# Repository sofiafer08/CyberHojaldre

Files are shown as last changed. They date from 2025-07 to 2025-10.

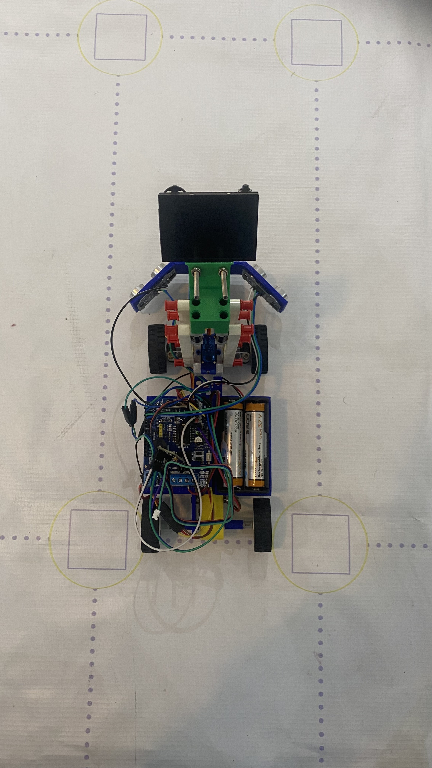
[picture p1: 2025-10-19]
V-photos/Top Angle.jpeg

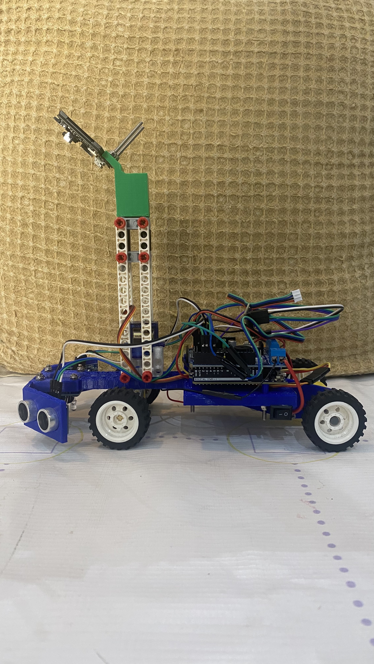
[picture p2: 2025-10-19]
V-photos/Right Angle.jpeg

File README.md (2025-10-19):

## CyberHojaldre - Future Engineers
<p>




encabezado github

## About Us

We are ***CyberHojaldre***, a dedicated team representing Thomas Jefferson School in the Future Engineers category of the WRO® 2025. Composed of Emilia Lever, Sofía Fernández, and Antonio Franco. This is our first year participating in this category and we are guided by our passion for robotics, comradery and are inspired by the 2025 season theme “The Future of Robots” —which explores how autonomous systems can shape tomorrow’s world, from smart cities and sustainable infrastructure to space exploration— we have embarked on an ambitious journey to design, build, and program an autonomous four-wheeled robotic vehicle capable of navigating a randomized course on its own. Together we have worked for months to bring our robot ***Captain ÑomÑom*** to life. Through the course of this competitions we have continuously refined our pre-existing skills, and have gotten the opportunity to expand our knowledge about electronics, mechanics, programming and teamwork.

>[!NOTE]
> We are always working on improving ***Captain ÑomÑom's*** performance! This means small tweaks are being made in every competition, which we may not be able to update immediately. 

marcos de fotos (1)

## Project Summary

Our robot, ***Captain ÑomÑom***, is designed to autonomously complete the driving challenge by detecting and avoiding obstacles in the track's controlled environment. The robot monitors track boundaries to ensure it stays within limits and maintains accurate navigation. It can also visually detect obstacles, allowing the robot to respond intelligently in real time by adjusting its path to avoid collisions depending on the obstacle's color. Beyond technical goals, one of our team's most important objectives is to enjoy the process, learn through experimentation and have fun building a robot that reflects both our creativity and our passion for robotics.

marcos de fotos (20)

## Past Projects

Before bringing ***Captain ÑomÑom*** to life, we had worked together to create a robot called ***POP*** -Short for People Is Nice-. It was able to complete the open course challenge and park in its starting position. He was built with the help of a 3D printed chassis and a sensor mount that complemented LEGO pieces. ***POP*** completed the course slowly yet accurately, but was unable to dodge obstacles. This is why we decided to start over with a new project a month before nationals. It would allow us to boost ***POP's*** ability allowing more speed, and a higher level performance. It involved replacing most components, programming from scratch, and changing the entire dynamic we had with our previous robot. This is how ***Captain ÑomÑom*** was born; thanks to an extensive creative process, and the merging of all our ideas. We are beyond excited for you to learn about all the specifications of ***Cap***. and hope you are able to see the technical growth required for the completion of this project. We keep ***POP*** in our hearts, and use him as inspiration for every cable wired and every line of code. Enjoy!

marcos de fotos (4)

## Team Members

| [**Sofía Fernández**](https://github.com/sofiafer08/CyberHojaldre/tree/main/Meet_the_Team#sofia-fernández) | [**Antonio Franco**](https://github.com/sofiafer08/CyberHojaldre/tree/main/Meet_the_Team#antonio-franco) | [**Emilia Lever**](https://github.com/sofiafer08/CyberHojaldre/tree/main/Meet_the_Team#emilia-lever) |
| :---: | :---: | :---: |
| *GitHub master, team spirit leader, and marketing director* | *Goofy designer and mechanics lead, invested in every part of the project* | *Silly, geeky programmer and electrician* | 
| <ins>16 years old</ins> | <ins>15 years old</ins> | <ins>16 years old</ins> |

## Table of Contents

* [`Code Explained`](./Code_Explained) This files contains an in-depth description on the way our program runs, and the process of making it. 
* [`Control Software`](./Control_Software) This file contains code of control software for all components which were programmed to participate in the competition.
* [`V-Photos`](./V-photos) Contains 6 photos of the vehicle (from every side, from top and bottom)
* [`Meet the Team`](./Meet_the_Team) Here you can find a short description of our team, who are our members, and several team photos. 
* [`Mobility Management`](./Mobility_Management) Inside it, are the strategic choices we made to achieve an efficient robot. 
* [`Models and Components`](./Models_&_Components) Here are all the 3D models designed by us to bring our robot to life, and a list of all its components. 
* [`Power and Sense Management`](./Power_&_Sense_Management) Inside this file is the description of the electrical distribution of our robot. 
* [`Schemes`](./Schemes) This file contains one or several schematic diagrams in form of JPEG, PNG or PDF of the electromechanical components illustrating all the elements (electronic components and motors) used in the vehicle and how they connect to each other.
* [`Vehicles Photos`](./V-photos/) Here you can find multiple photos of our robot taken from different perspectives (from every side, top and bottom. 
* [`Performance Video`](./Video) This file contains the performance video of our robot during the open course.

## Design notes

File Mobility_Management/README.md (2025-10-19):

# Mobility Management

## General Vehicle Design

The robotic vehicle is constructed upon a **3D printed PETG chassis**. It's powered through the rear axle using a **3V–6V Dual Axis TT Gear Motor** and steered with a **SG90 9g Micro Servo**. It counts with two **HC-SR04 Ultrasonic Distance Sensors** to detect the track's walls in order to avoid collisions, a **HUSKYLENS Smart Vision Sensor** to detect incoming traffic signs and identify their color and a **TCS3200 Color Sensor Module** which serves as a backup for the camera. All systems are controlled by an **Arduino UNO R4 WiFi** with a **Module L298P Motor Shield HW-723**.

## Drivetrain

### Rear-Wheel Drive

We power our drivetrain using a **3V–6V Dual Axis TT Gear Motor**, which is directly connected to the vehicle's rear axle. Our rear axle is responsible for the forward and backward motion on our robot. This rear wheel drive design eliminates the necessity for complex systems such as constant velocity (CV) joints or external gearboxes without sacrificing torque, speed, and traction; resulting in a reliable and easy to repair robot.

marcos de fotos (10)

### Steering

We use an **Ackermann steering** built using LEGO parts. This steering system is proven to be one of the most efficient and reliable which is demonstrated by its years of use in the automotive industry. The Ackermann principle ensures that a vehicle's inner front wheel turns at a greater angle than the outer front wheel during a turn, allowing both wheels to trace concentric circles around a single virtual pivot point. We control the steering using degrees thanks to the **SG90 9g Micro Servo**, which makes it easier to program and improves the robot's accuracy. This steering system also provides a wide range of movement, making the vehicle highly maneuverable.

marcos de fotos (11)

## 3D Printed Parts

### Chassis

We use a custom **3D printed PETG chassis** designed using Fusion 360. This vehicle frame is custom fitted with a space for our **two Slot 18650 Battery Holder**, an **Arduino UNO R4 WiFi** holder, a bracket for our **3V–6V Dual Axis TT Gear Motor**, a LEGO compatible 3x9 Technic axle hole plate to secure our steering's **SG90 9g Micro Servo's LEGO mount** and the **HUSKYLENS Smart Vision Sensor's** mount, holes for our **HC-SR04 Ultrasonic Distance Sensors** and a mount for our **TCS3200 Color Sensor Module**. This simple design gives us ease of repair, high ground clearance and torsional rigidity. It's an effective design which adapts to our robot's needs.

For more information, [*click here*](https://github.com/sofiafer08/CyberHojaldre/blob/main/Models_%26_Components/Chassis.stl) to open the Chassis Interactive stl.

marcos de fotos (5)

### Rear Axle Adapters

In order to directly connect our **3V–6V Dual Axis TT Gear Motor** to the vehicle's rear axle, we designed two **3D printed PETG adapters**. From one side, the adapter is able to connect to the **3V–6V Dual Axis TT Gear Motor's** axle, while from the other its able to couple with a LEGO Technic axle, allowing us to use LEGO wheels and tires to provide traction.

For more information, [*click here*](https://github.com/sofiafer08/CyberHojaldre/blob/main/Models_%26_Components/tt_Motor_Axle.stl) to open the Motor Axle Interactive stl

marcos de fotos (7)

### Camera Mount

The HUSKYLENS Smart Vision Sensor is installed in a 3D printed PETG camera mount. This mount allows us to have a greater height and position the camera at a 45° angle during the robot’s testing in order to enhance the range and accuracy. We connect it to the chassis LEGO pins, as both 3D printed pieces have LEGO compatibility. This modular piece amplifies the number of uses our camera has, changing the robot’s capacities.

For more information, [*click here*](https://github.com/sofiafer08/CyberHojaldre/blob/main/Models_%26_Components/HuskyLens_Mount.stl) to open the HuskyLens Mount Interactive stl.

marcos de fotos (8)

### Servo LEGO Mount

We also used the bottom part of a **SG90 9g Micro Servo LEGO mount** designed by **wilix from Thingyverse**. This mount enabled us to connect the servo's axle to our LEGO steering, giving us a great mix of efficiency and compatibility.  

For more information, [*click here*](https://www.thingiverse.com/thing:4303585) to visit the wilix's Thingyverse page.

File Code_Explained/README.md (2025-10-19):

## Open Challenge Programming

For our previous robot we programmed using MakeCode for microbit. It consisted of a simple code that would rotate the servo to 210 degrees if the left ultrasonic sensor percieved a distance less than 45cm. The same would happen with the right ultrasonic sensor, but in that case the servo will rotate to 150 degrees. In the case that both sensors read a distance greater than 30cm, the servo was set to 180 degrees and it would continue its straight path. Once the time variable ended, the DC motor would be stopped, and our robot would park in the position it started. 

Since we developed **Captain ÑomÑom**, We have now programmed a new code that includes other components that facilitate Cap.'s cruising. 

*   The code begins by establishing where all the physical components like motors and sensors are connected. It also sets important constants that act as the robot's rules of operation:

      *   **Max Sequences:** Dictates the total number of times the robot will perform  the color detection and then turn. When it reaches this number Cap. will shut down.
      *   **Reset Delay:** The brief pause the robot takes after reacting to a color before it's ready for the next one. This ensures Cap. will read only one color when he gets to the turns. Without it, he would detect both blue and orange and would turn in oppossite directions, steering him away from his course.
      *    **Shutdown Delay:** The amount of time the robot waits after its final sequence before turning off its motor. With this fuction, we can ensure Cap. reaches it original position and doesnt stop suddenly in the middle of a turn.
      *  **Steering Range:** The servo motor's movement is limited to a safe range where we have the MAX and MIN angles, 108 and 78 degrees accordingly, to prevent the robot from making overly sharp turns. 

*   **Sensors & Perception:**
    *   The robot relies on two main sensing systems that work together:
        *   **HuskyLens Camara:** This is the primary component of the code. It is trained to recognize organge and blue to perform the turns and not rely solely on ultrasonic sensors. When it detects blue, it commands a left turn. When it detects oragne, it commands a right turn.
        *   **Ultrasonic Sensors:** These act as a secondary system for obstacle avoidance. If Cap. gets too close to a side of the walls, the ultrasonic sensors will help him stay centered, and avoid crashing. 

*   **Startup Sequence:**
    *   When powered on, the robot pauses for 3 seconds to ensure all systems are ready.
    *   It then checks for the HuskyLens camera and prepares it for color detection.

*   **Main Operation Loop:**
    *   The core of the code is a loop that constantly checks a specific order of events:
        1.  **Shutdown Check:** It first checks if the maximum number of sequences has been reached to begin the shutdown process. This number is 12, seeing as Cap. would need to detect the color 12 times in order to complete three full rounds. 
        2.  **Color Detection:** If it hasn't reached the max number of sequences (12 detections), it prioritizes looking for the colored lines. When a color is spotted, it executes the corresponding turn, atllies up the sequence, and temporarily pauses further color detection for 2 seconds.
        3.  **Obstacle Avoidance:** While paused for color detection (or when no color is seen), the ultrasonic sensors remain active to avoid bumps.
        4.  **Reset:** After the reset delay, the robot centers its wheels and resumes looking for colors, continuing the cycle until its task is complete.

* Once it completes the three rounds the servo is set back to 90 degrees so that it will go straight for a few seconds more and park in its original position bringing us to the end of our Open Course Code. 

## Obstacle Challenge Programming

### **Course Explanation: Obstacle Avoidance & Navigation**

The code begins by establishing where all the physical components like motors, sensors, and camera are connected. It also sets important constants that act as the robot's rules of operation:

*   **Max Sequences:** Dictates the total number of times the robot will perform a primary color detection and turn sequence. When it reaches this number, the robot will shut down.
*   **Color Detection Pause:** A 6-second period after detecting a blue or orange line where the robot ignores further blue/orange detections. This ensures it completes its turn and reverse maneuver without being interrupted. During this pause, it can still detect and react to red and green obstacles.
*   **Steering Angles:** The robot uses two sets of turning angles. **Sharp turns** are used during the initial setup and for quick ultrasonic obstacle avoidance. **Mild turns** are used for the main course navigation, providing smoother and more controlled turns around obstacles and after detecting lines.
*   **Ultrasonic Threshold:** The minimum distance, in centimeters, at which the robot considers an object an obstacle and will initiate an avoidance turn.

*   **Sensors & Perception:**
    *   The robot relies on two main sensing systems that work together:
        *   **HuskyLens Camera:** This is the primary sensor for navigation. It is trained to recognize four colors:
            *   **Blue & Orange:** These are the *primary navigation lines*. They signal the robot to execute a turn sequence, bump into the wall behind it, and then continue, effectively moving it to the next section of the course.
            *   **Red & Green:** These act as *virtual obstacles*. When detected, the robot performs an avoidance maneuver by backing up and turning left and right to navigate around them.
        *   **Ultrasonic Sensors:** These act as a secondary, physical safety system for obstacle avoidance. If the robot gets too close to a wall or object on its left or right side, these sensors will command a mild turn to keep it centered and avoid crashes.

*   **Startup Sequence:**
    *   When powered on, the robot initializes its motors, servo, and sensors.
    *   It performs an initial environmental check using the ultrasonic sensors to ensure it has space to operate.
    *   It then checks for the HuskyLens camera and prepares it for color detection.

*   **Main Operation Loop:**
    *   The loop constantly checks a specific order of events:
        1.  **Shutdown Check:** It first checks if the maximum number of sequences has been reached to begin the shutdown process.
        2.  **Continuous Ultrasonic Monitoring:** The ultrasonic sensors are the least important part of the code. If a wall is detected, the robot turns mildly away from it, and then continues forward. This is done to avoid walls in case Cap. gets too close to them. This is vital to ensure the HuskyLens has a clear view of all the obstacles. If it's too close to one side, it's possible he’ll miss the detection of certain obstacles.
        3.  **Color Detection & Reaction:** The robot simultaneously looks for colors. He has two given instructions in case he detects one of the two possible sets of colors:
            *   **Blue/Orange:** The robot will continue a forward motion for a few seconds longer, sort of a delay before turning. This is so that he has advanced enough to turn and bump into the wall behind him. He first turns in the corresponding direction, then reverses to bump into the wall. This way, he can always center himself and is awa.re of all the objects in front of him. This prevented him from turning too sharply or too widely and missing obstacles around him. When completing this sequence, he also tallies it up so as to keep track of how many laps are missing. Once he reaches 12, he will stop. Lastly, after the detection of one of the colored lines, he enters a pause period where it ignores further blue/orange lines so as to not detect the same line when going forward again.

            *   **Red/Green:** This feature allows him to avoid obstacles. When detecting either green or red, he stops, reverses briefly so as to not bump into the obstacle, and then performs a sequenced turn (left-then-right or right-then-left) to navigate around the virtual obstacle before continuing forward. When he makes this maneuver he ensures the obstacle is avoided, but also places himself back in his path.

*   Once the robot completes its maximum number of sequences (12), it stops its motor, bringing the course run to a complete end.

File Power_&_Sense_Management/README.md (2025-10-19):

Power and Sensor Management
===

## Power Source

### Batteries

The power source of ***Captain ÑomÑom*** are **two 18650 Rechargeable Lithium-Ion Batteries**, each with a nominal voltage of **3.7Vdc** and a storage capacity of **2800 mAh**. They are coupled on a **two slot 18650 Battery Holder** which is connected to the VMS (power input) and GND (negative ground connection) ports on our **Module L298P Motor Shield HW-723**. The shield regulates the voltage to 5Vdc before supplying power to our **Arduino UNO R4 WiFi**. Then, through our shield's 5V ports, we supply both of our **HC-SR04 Ultrasonic Distance Sensors**, our **HUSKYLENS Smart Vision Sensor**, our **TCS3200 Color Sensor Module**, our **SG90 9G Micro Servo** and our **3Vdc ~ 6Vdc Dual Axis TT Gear Motor**.

rechargeable-li-ion-battery 200

**Key Specifications:**
* **Nominal Voltage:** 3.6 Vdc ~ 3.7 Vdc
* **Nominal Capacity:** 2800 mAh
* **Cycle Life:** ~500 cycles (to 80% capacity)

For more information, [*click here*](https://www.tinytronics.nl/product_files/004721_TENPOWER_INR18650-28HE_datasheet.pdf) to open the 18650 Rechargeable Lithium-Ion Battery's datasheet.

## Sensors

### Ultrasonic Sensors

We used two **HC-SR04 Ultrasonic Distance Sensors**. Each sensor provides **2cm to 400cm** of non-contact measurement functionality with a ranging accuracy that can reach up to **3mm**. Each HC-SR04 module includes an ultrasonic transmitter, a receiver and a control circuit. We placed a sensor on each side (left and right) of our autonomous vehicle. Their purpose is to detect the track's walls in order to avoid collisions.

ultrasonic sensor 200

**Key Specifications:**
* **Operating Voltage:** 3.3Vdc ~ 5Vdc
* **Quiescent Current:** <2mA
* **Operating Current:** 15mA
* **Operating Frequency:** 40KHz
* **Operating Range & Accuracy:** 2cm ~ 400cm ( 1in ~ 13ft) ± 3mm
* **Sensitivity:** -65dB min
* **Sound Pressure:** 112dB
* **Effective Angle:** 15°
* **Connector:** 4-pins header with 2.54mm pitch
* **Dimension:** 45mm x 20mm x 15mm
* **Weight:** 9g

For more information, [*click here*](https://www.handsontec.com/dataspecs/HC-SR04-Ultrasonic.pdf) to open the HC-SR04 Ultrasonic Distance Sensor's datasheet.

### Color Sensor

We used a **TCS3200 Color Sensor Module**. The sensor can detect a wide variety of colors based on their wavelength. This sensor is specially useful for color recognition projects such as color matching and color sorting. Each TCS3200 module includes an array of photodiodes, filters for different colors, and a control circuit. Its purpose is to detect the diagonal lines which merge on the track's walls in order to make precise turns.

color sensor 200

**Key Specifications:**
* **Operating Voltage:** 2.7Vdc ~ 5.5Vdc
* **Photodiodes:** 64 total (16 red, 16 green, 16 blue, 16 clear)
* **Operating Range & Accuracy:** Best at 1–3 cm from the object
* **Extras on module:** Includes 4 white LEDs for consistent illumination

For more information, [*click here*](https://www.mouser.com/catalog/specsheets/tcs3200-e11.pdf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) to open the TCS3200 Color Sensor Module's datasheet.

>[!NOTE]
> We are currently not implementing this sensor as part of our code. We decided to replace its original function with the HuskyLens. Nonetheless, it still remains as part of our robot in case a minor inconvenience occurs. 
### HuskyLens Camera

We used a **HUSKYLENS Smart Vision Sensor**. This sensor can detect and recognize objects, faces and colors using built-in AI algorithms. It is especially useful for projects involving computer vision, such as object tracking and autonomous navigation. Each HUSKYLENS module includes a camera, a processor for AI functions and an interface with a digital display and buttons. Its purpose is to detect incoming traffic signs and identify their color in order to indicate the vehicle side of the lane it must follow in the obstacle challenge.

Husky lens 200

**Key Specifications:**
* **Processor:** Kendryte K210
* **Image Sensor:** OV2640 (2.0 Megapixel Camera)
* **Operating Voltage:** 3.3Vdc ~ 5Vdc
* **Current Consumption (TYP):** 320mA 3.3Vdc, 230mA 5Vdc (face recognition mode; 80% backlight brightness; fill light off)
* **Connection Interface:** UART, I2C
* **Display:** 2in IPS screen with 320 x 240 resolution
* **Built-in Algorithms:** Face Recognition, Object Tracking, Object Recognition, Line Tracking, Color Recognition, Tag Recognition
* **Dimension:** 52mm x 44.5mm

For more information, [*click here*](https://www.farnell.com/datasheets/3178377.pdf) to open the HUSKYLENS Smart Vision Sensor.

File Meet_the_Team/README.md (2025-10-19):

Meet the members of our team
===

## Sofia Fernández

<p align='justify'>My name is Sofia Fernandez, I'm a 16-year-old girl from Honduras currently living in Panama. I moved here last year in search of better opportunities, and since then, I've discovered a passion for robotics and everything related to STEM. This new environment has inspired me to keep learning, growing, and exploring all the possibilities within science, technology, engineering, and math. I'm always looking for ways to expand my knowledge and take on new challenges in the STEM world.</p>  

marcos de fotos (14)

## Antonio Franco 

<p align='justify'>My name is Antonio Franco, I'm a 15-year-old boy born in Panama. I've shared a passion for STEM and engineering from an early age, making my career in robotics very vast. In my path, I've discovered that Computer Aided Design or CAD is my main talent, which I've incorporated in each one of my projects. Competitions like FRC or WRO are constant challenges for my skills, which inspire me each day to aim higher and to prove I'm capable of achieving success. STEM always keeps me growing and improving, and I always look forward to challenging myself with each project.</p>  

marcos de fotos (19)

## Emilia Lever 

<p align='justify'>Hello! My name is Emilia, and I´m 16-years-old. I have always enjoyed participating in as many activities as possible, which led to the development of a variety of hobbies such as knitting, dancing, theater, debate, etc. As I've dipped my toes into the different pools of extracurriculars, I discovered a deep love towards the STEM community. I have since been a part of many robotic groups in a diverse range of competitions with a specific passion for the math olympics, even reaching silver and bronze medals. I hope to continue expanding my knowledge and skills with the help of my mentors and teammates, and will forever encourage people to give the STEM world a chance to win their hearts over.</p>  

marcos de fotos (16)

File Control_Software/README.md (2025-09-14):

Control software
====

This directory contains the code for both the Open and Obstacle Course. You can find the code written in C++ coded in the platform ARDUINO.IDE.
An explanation about our coding decisions can be found in [Code Explained](https://github.com/sofiafer08/CyberHojaldre/tree/main/Code_Explained) .

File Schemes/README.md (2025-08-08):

Electromechanical diagrams
====

This directory contains one schematic diagrams in the form of a PNG of the electromechanical components illustrating all the elements (electronic components and motors) used in the vehicle and how they connect to each other.

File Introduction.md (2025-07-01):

Future Engineers
====

* We are Emilia Lever, Sofia Fernandez, and Antonio Franco, a dedicated team representing the Thomas Jefferson School in the Future Engineers category of the WRO® 2025. Guided by our passion for robotics and inspired by the 2025 season theme “The Future of Robots”—which explores how autonomous systems can shape tomorrow’s world, from smart cities and sustainable infrastructure to space exploration—we have embarked on an ambitious journey to design, build, and program an autonomous four-wheeled robotic vehicle capable of navigating a randomized course on its own.

## Content

* `t-photos` contains 2 photos of the team (an official one and one funny photo with all team members)
* `v-photos` contains 6 photos of the vehicle (from every side, from top and bottom)
* `video` contains the video.md file with the link to a video where driving demonstration exists
* `schemes` contains one or several schematic diagrams in form of JPEG, PNG or PDF of the electromechanical components illustrating all the elements (electronic components and motors) used in the vehicle and how they connect to each other.
* `src` contains code of control software for all components which were programmed to participate in the competition
* `models` is for the files for models used by 3D printers, laser cutting machines and CNC machines to produce the vehicle elements. If there is nothing to add to this location, the directory can be removed.
* `other` is for other files which can be used to understand how to prepare the vehicle for the competition. It may include documentation how to connect to a SBC/SBM and upload files there, datasets, hardware specifications, communication protocols descriptions etc. If there is nothing to add to this location, the directory can be removed.

## Robot Objectives

## Mobility Management

Our robot, "POP", short for People is nice, works with the help of two motors. For the movement of the rear-axle we implemented a red "GeekServo" direct current (DC) motor, we chose it since it has a strong online community that already implements this motor using micro:bit software and hardware. It also has LEGO compatability, making it easier to adapt to our design. Our robot POP has a gray "GeekServo" servo motor as well. This controls the front-axle and provides the high-precision that is needed. This motor allows us to program it using degrees, which fits our team's need for accuracy.

The design of our chassis was made from scratch using Autodesk Fusion 360. Since the motors we agreed upon were compatible with LEGO components, it was only natural that our design was based on these same pieces. We have a simple structure inspired on a ladder-frame chassis, since our main objectives can be accomplished with a reliable base.

## Power and Sensor Management
## Obstacle Management
## Open Challenge Programming
## Programming Challenge Obstacles
## Components 

POP has a variety of parts that make up both his hardware and software. This includes:

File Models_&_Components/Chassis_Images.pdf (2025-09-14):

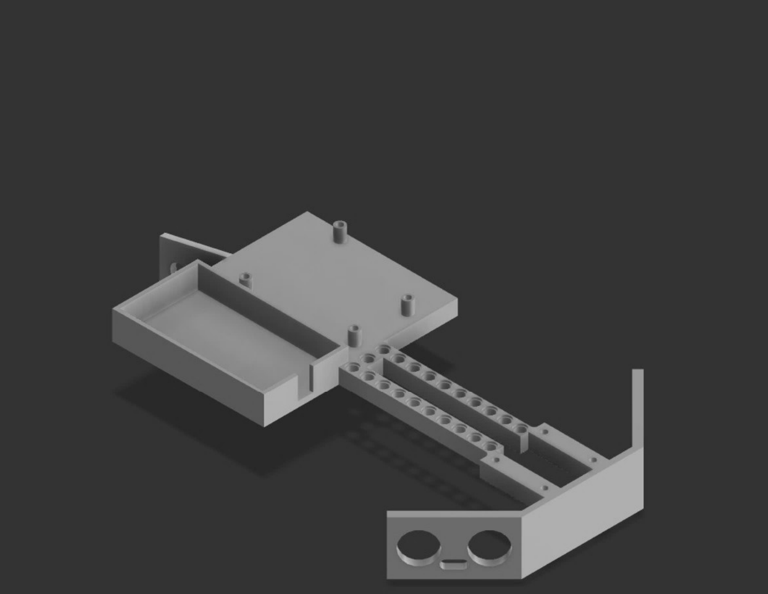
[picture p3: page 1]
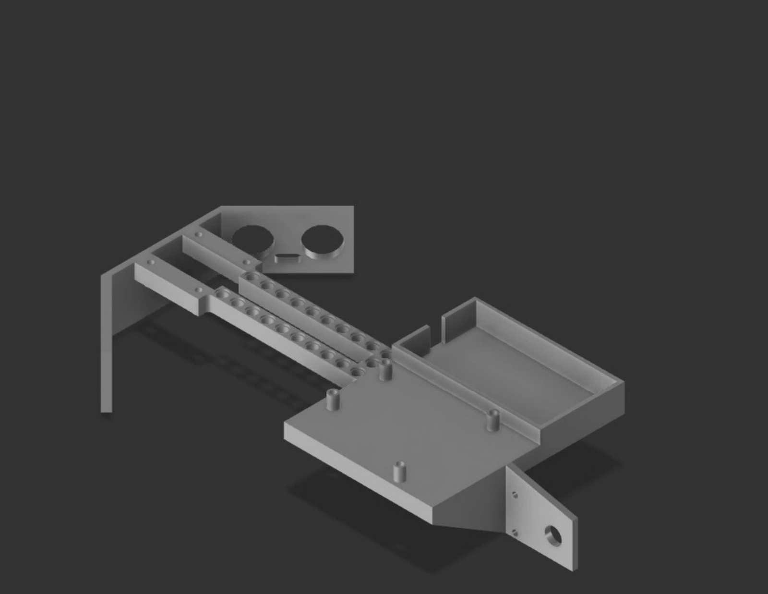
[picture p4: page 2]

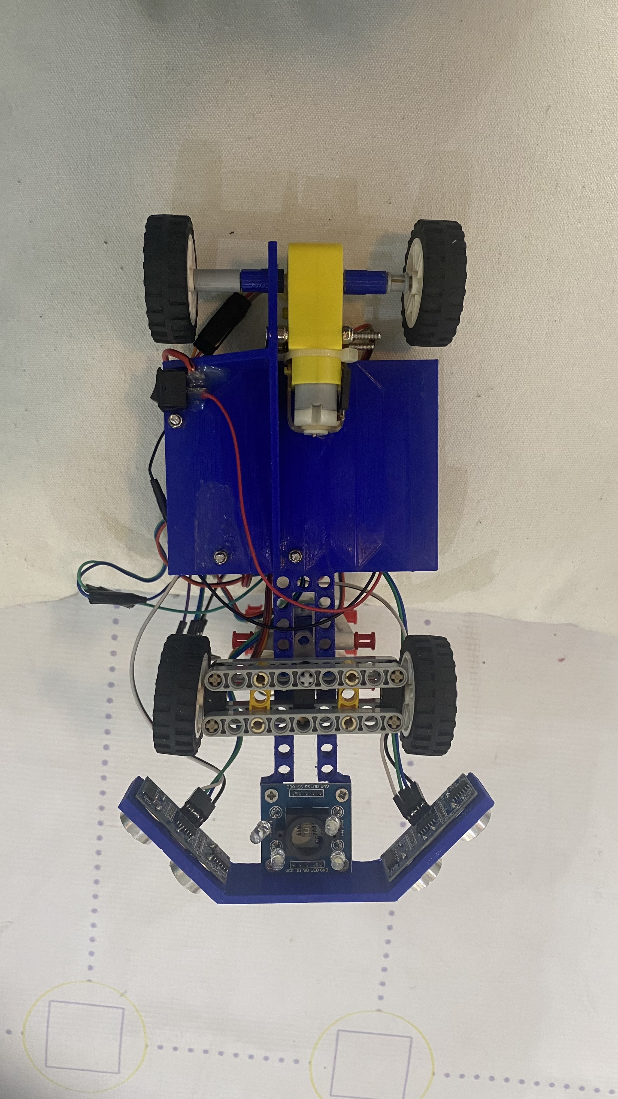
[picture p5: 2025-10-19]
V-photos/Bottom Angle.jpeg

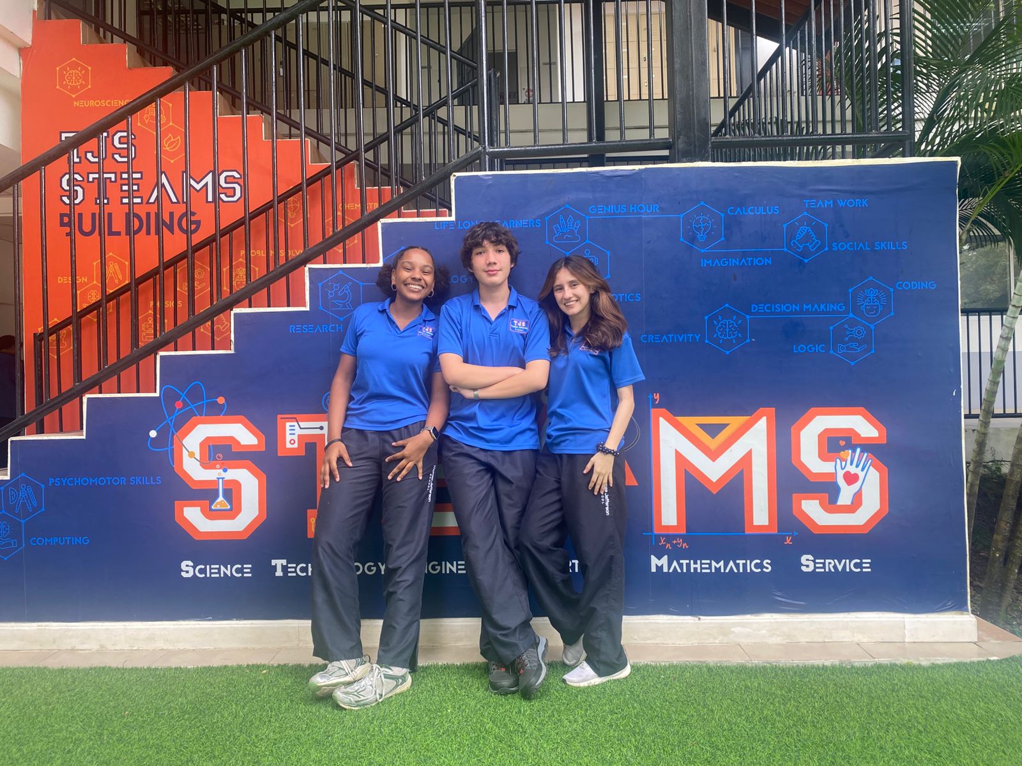
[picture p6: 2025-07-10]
Meet_the_Team/Formal Photo.jpg

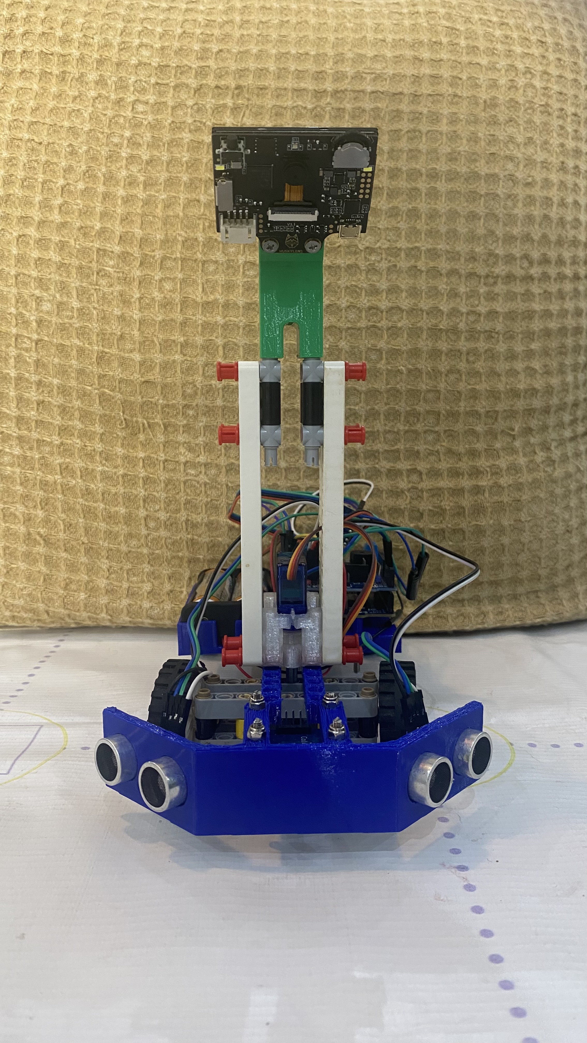
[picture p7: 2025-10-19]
V-photos/Front Angle.jpeg

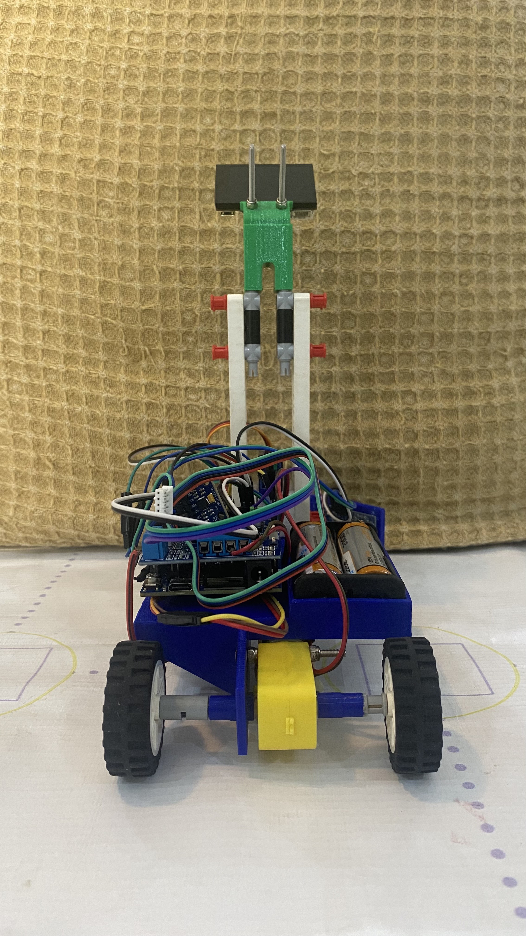
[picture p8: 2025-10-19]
V-photos/Rear Angle.jpeg

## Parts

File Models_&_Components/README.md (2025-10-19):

# Models & Components

## 3D Models 

* [Chassis Images](./Chassis_Images.pdf)
* [Chassis Interactive stl](./Chassis.stl)
* [Image of Motor Axle](./tt_Motor_Axle.jpeg) 
* [Motor Axle Interactive stl](./tt_Motor_Axle.stl)
* [Image of HuskyLens Mount](./HuskyLens_Mount_Image.png)
* [HuskyLens Mount Interactive stl](./HuskyLens_Mount.stl)
* [Servo LEGO Mount - Thingyverse page](https://www.thingiverse.com/thing:4303585)
  
## List of components:

| Quantity | Name | Utility | Voltage | Image | 
|---|---|---|---|---|
| 1 | **TCS3200 Color Sensor Module** | Detects the diagonal lines that merge on the track's walls in order to make precise turns. *After a series of changes, we decided not to use the color sensor.* | 2.7Vdc ~ 5.5Vdc | color sensor 356 |
| 1 | **HUSKYLENS Smart Vision Sensor** | Detects incoming traffic signs and lines in the track and identifies their color in order to indicate our vehicle's side of the lane it must follow in the obstacle challenge. | 3.3Vdc ~ 5Vdc | Husky lens 356 |
| 2 | **HC-SR04 Ultrasonic Distance Sensors** | Detects the track's walls in order to avoid collisions. | 3.3Vdc ~ 5Vdc | actual sensor hc foto|
| 1 | **Arduino UNO R4 WiFi** | Acts as the central control unit for the vehicle, enabling communication and processing of commands. | 6 V-24 V | Arduino r4 356|
| 1 | **Module L298P Motor Shield HW-723** | Facilitates the connection and control of all components to the Arduino board and contains the motor's controller. | 4.8V ~ 35V | arduino l298p 356| 
| 1 | **3V–6V Dual Axis TT Gear Motor** | Powers the movement of the vehicle’s rear wheels, providing the necessary torque for driving. |  3Vdc ~ 6Vdc |Motor amarillo 356|
| 1 | **SG90 9g Micro Servo** | Controls the steering mechanism, adjusting the front wheels to guide the vehicle’s direction. | 3Vdc ~ 6Vdc | not_micro_servo

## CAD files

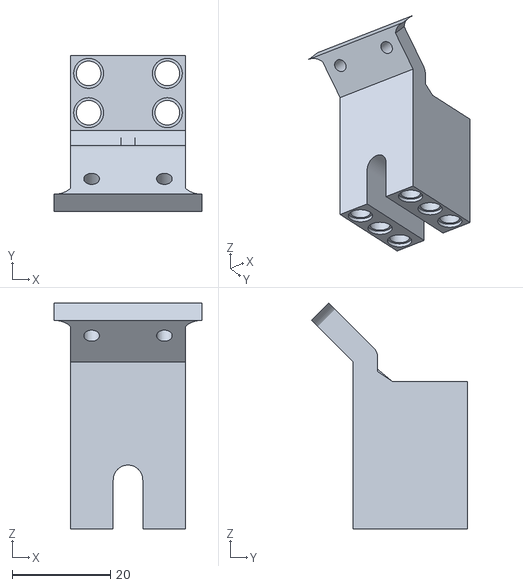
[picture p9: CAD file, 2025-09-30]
Models_&_Components/HuskyLens_Mount.stl
30.0 x 31.8 x 46.0

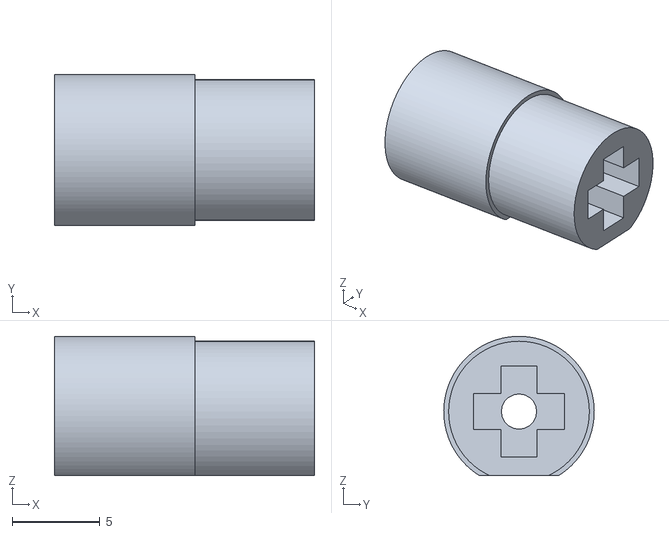
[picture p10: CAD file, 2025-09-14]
Models_&_Components/tt_Motor_Axle.stl
14.8 x 8.56 x 7.92

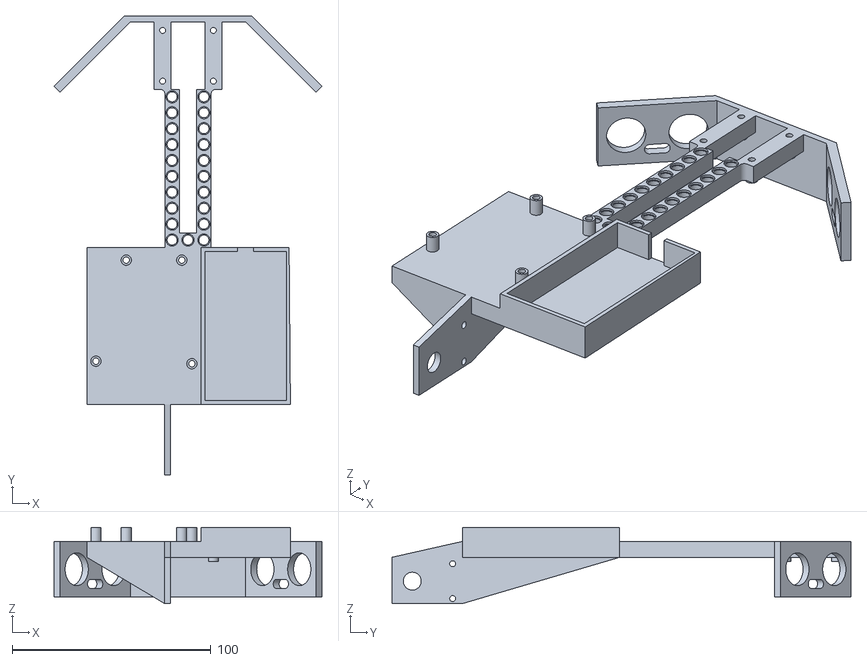
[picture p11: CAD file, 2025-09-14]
Models_&_Components/Chassis.stl
134.7 x 230.8 x 38.2

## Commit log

2025-08-07 Rename Ultrasonic Sensor Support drawing v1.pdf to Ultrasonic Sensor Support drawing v1.pdf
2025-08-07 Rename Ladder Chassis drawing v1.pdf to Ladder Chassis drawing v1.pdf
2025-08-08 Update and rename Chasis.stl to Chasis.stl
    [Chasis.stl]
2025-09-14 Rename WhatsApp Image 2025-09-11 at 6.29.23 PM (1).jpeg to Chassis_Image_1
2025-09-14 Rename WhatsApp Image 2025-09-11 at 6.29.23 PM.jpeg to Chassis_Image_2
2025-09-14 Create Chassis_Images
2025-10-19 Replace camera mount image in README
    Updated image in README with a new photo of the camera mount.
2025-10-19 Replace image in README for rear-wheel drive
    Updated image source in README for rear-wheel drive section.
2025-10-19 Document SG90 Micro Servo LEGO mount usage
    Added information about the SG90 9g Micro Servo LEGO mount and its source.
2025-10-19 Update servo description and image in README
2025-10-19 Revise TCS3200 Color Sensor Module description
    Updated the description for the TCS3200 Color Sensor Module to indicate it will not be used after recent changes.
2025-10-19 Refactor obstacle challenge code for clarity and efficiency
    Refactored obstacle challenge code to improve structure and functionality, including updates to servo and motor control, color detection, and ultrasonic sensor handling.
2025-10-19 Refactor color detection and servo control logic
    Refactor color detection logic and add handling for servo movements based on detected colors. Introduce new constants for servo positions and color detection thresholds.
2025-10-19 Add Thingiverse link for HuskyLens Mount STL
    Added a link to the HuskyLens Mount Interactive STL on Thingiverse.
2025-10-19 Update README with new Servo LEGO Mount link
2025-10-19 Update link text for Servo LEGO Mount
2025-10-19 Clarify description of L298P Motor Shield
